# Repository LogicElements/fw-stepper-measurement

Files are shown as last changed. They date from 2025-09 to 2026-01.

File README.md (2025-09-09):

# Stepper Measurement System

This repository contains hardware and firmware for the Stepper Measurement System:
 - Hardware board 
 - Bootloader
 - Application firmware
 - Python test scripts
 - Documentation

# Register map

Modbus register map and internal memory structure is managed using Excel generator
./Documents/PrecRtdSim.xlsm. This worksheet contains several VBA scripts that
translates defined variables into firmware local storage definition, firmware modbus
register map, python class definition and json register map definition.

Some documentation can be found in ./Documents/wiki.

> [!NOTE]
> Opening excel worksheet with macros may show some kind of warning

# Programming bootloader

In order to flash bootloader firmware with serial number, proceed as follows:
- connect power and st-link
- edit ./Binary/STLink-program.bat with serial number prefix and binary names
- run `./Binary/STLink-program.bat x` where `x` is serial number to program 

Any further debugging can be done using IDE.

# Python tools

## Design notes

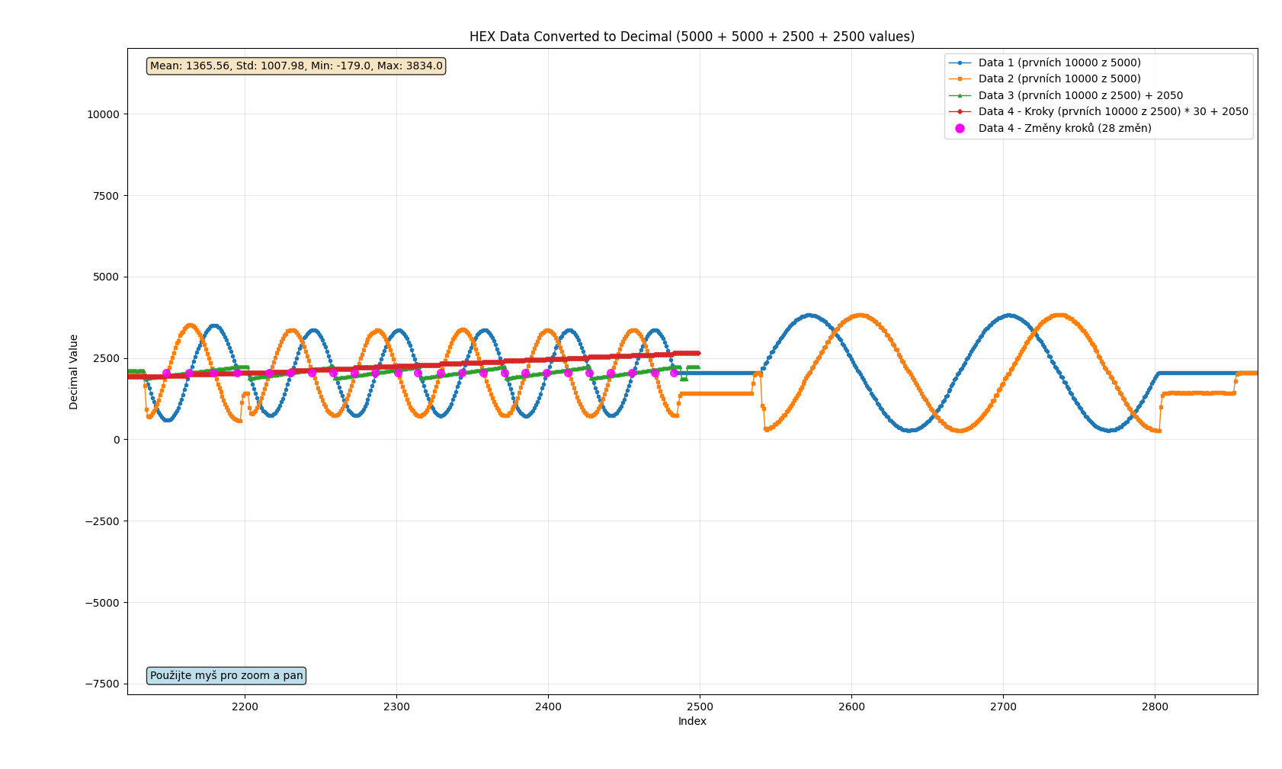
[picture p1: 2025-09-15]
Documents/img/doraz_komplet.png

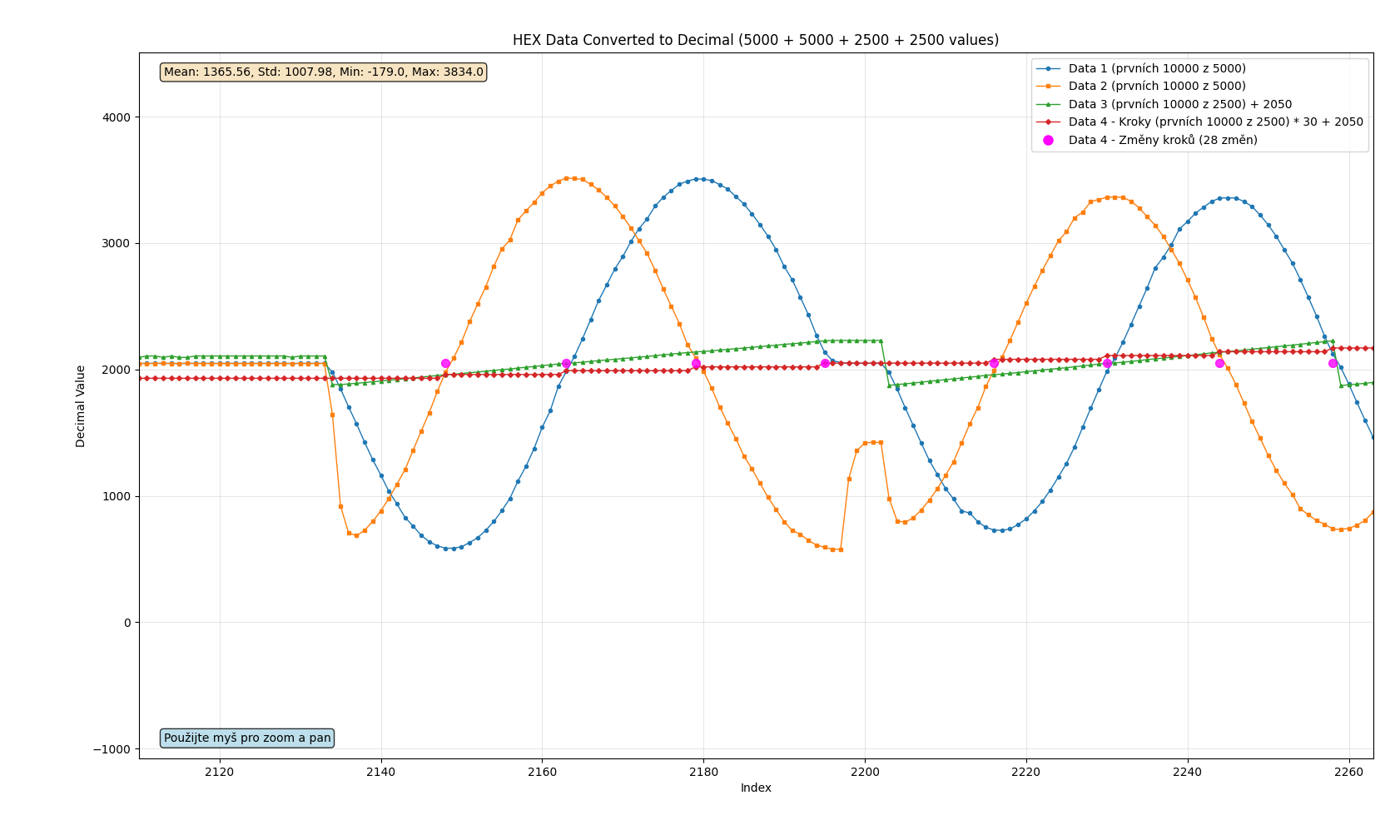
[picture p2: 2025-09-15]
Documents/img/doraz_cast_prubehu.png

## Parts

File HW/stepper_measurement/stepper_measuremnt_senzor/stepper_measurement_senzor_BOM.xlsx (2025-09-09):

Comment | Description | Designator | Footprint | LibRef | Quantity | Link
0.1uF | Capacitor | C4.1, C4.2, C4.3, C4.4, C6.1, C6.2, C6.3, C6.4, C7.1, C7.2, C7.3, C7.4 | SMD_CAPACITOR_0805 | Capacitor | 12 | https://cz.mouser.com/ProductDetail/KYOCERA-AVX/KAM21BR71H104JT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
 | Diode Schottky | D2.1, D2.2, D2.3, D2.4, D3.1, D3.2, D3.3, D3.4 | SMD_DO-214AChttps://cz.mouser.com/ProductDetail/Comchip-Technology/CZRA4728-HF?qs=2qJf6qQ4IOKpvgiXKvPuNQ%3D%3D | Diode_Schottky | 8 | https://cz.mouser.com/ProductDetail/Comchip-Technology/CZRA4728-HF?qs=2qJf6qQ4IOKpvgiXKvPuNQ%3D%3D
M50-3202045 | 1.27mm (0.05) Pitch DIL Horizontal Throughboard Socket Assembly, gold, 20+20 contacts | J1 | HARWIN_M50-3202045 | M50-3202045 | 1 | https://cz.mouser.com/ProductDetail/Harwin/M50-3202045?qs=Jph8NoUxIfXFh9Xgg1OEGQ%3D%3D
H2175-05 |  | J4, J5, J6, J7 | HARWIN_H2175-05 | H2175-05 | 4 | https://cz.mouser.com/ProductDetail/Harwin/H2175-05?qs=ulE8k0yEMYbNbWL6Op%252Bk7A%3D%3D
M50-3530242 | 1.27mm (0.05) Pitch SIL Vertical Throughboard Pin Header, selective gold + tin, 2 contacts | J8, J9, J10.1, J10.2, J10.3, J10.4 | HARWIN_M50-3530242 | M50-3530242 | 6 | https://cz.mouser.com/ProductDetail/Harwin/M50-3530242?qs=%252BdQmOuGyFcFfqfwYQe%2FxZw%3D%3D
Red | LED | LED1 | SMD_LED_0805 | LED | 1 | https://cz.mouser.com/ProductDetail/Wurth-Elektronik/150080RS75000
0.130 | Resistor | R3.1, R3.2, R3.3, R3.4 | SMD_RESISTOR_1206 | Resistor | 4 | https://cz.mouser.com/ProductDetail/TE-Connectivity-CGS/RLC73K2BR13FTDF
10K | Resistor | R10.1, R10.2, R10.3, R10.4, R11.1, R11.2, R11.3, R11.4 | SMD_RESISTOR_0805 | Resistor | 8 | https://cz.mouser.com/ProductDetail/TE-Connectivity-Holsworthy/4-2176238-9
1K | Resistor | R12, R15.1, R15.2, R15.3, R15.4 | SMD_RESISTOR_0805 | Resistor | 5 | https://cz.mouser.com/ProductDetail/Panasonic/ERA-6AED102V
6.5K | Resistor | R13.1, R13.2, R13.3, R13.4 | SMD_RESISTOR_0805 | Resistor | 4 | https://cz.mouser.com/ProductDetail/Panasonic/ERJ-HP6F6491V
12.4K | Resistor | R14.1, R14.2, R14.3, R14.4 | SMD_RESISTOR_0805 | Resistor | 4 | https://cz.mouser.com/ProductDetail/Panasonic/ERJ-UP6F1242V
50K | Resistor | R16.1, R16.2, R16.3, R16.4, R17.1, R17.2, R17.3, R17.4 | SMD_RESISTOR_0805 | Resistor | 8 | https://cz.mouser.com/ProductDetail/Vishay-Draloric/RCA08056K49FKEA
47K | Resistor | R18.1, R18.2, R18.3, R18.4, R19.1, R19.2, R19.3, R19.4 | SMD_RESISTOR_0805 | Resistor | 8 | https://cz.mouser.com/ProductDetail/Bourns/CRS0805-FX-4701ELF
INA240A1D | -4 to 80V, bidirectional, ultra-precise current sense amplifier with enhanced PWM rejection 8-SOIC -40 to 125 | U2.1, U2.2, U2.3, U2.4 | SOIC127P599X175-8N | INA240A1D | 4 | https://cz.mouser.com/ProductDetail/Texas-Instruments/INA240A1D?qs=u4fy%2FsgLU9OqCdP7Ou6Gjw%3D%3D
INA826AID | Precision, 200-Î¼A Supply Current, 36-V Supply Instrumentation Amplifier | U3.1, U3.2, U3.3, U3.4 | SOIC127P599X175-8N | INA826AID | 4 | https://cz.mouser.com/ProductDetail/Texas-Instruments/INA826AID?qs=RqytGdBYyUH0CDtkCzl1iw%3D%3D
 |  |  |  |  | 81

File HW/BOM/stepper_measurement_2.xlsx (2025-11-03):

Name | Description | Designator | Quantity | Supplier 1
2.2uF | Capacitor | C1, C24 | 2 | https://cz.mouser.com/ProductDetail/TDK/C2012X7R2A225K125AC?qs=17ckDYBRdekDf%2FwiwHq7Mg%3D%3D
100nF | Capacitor | C2, C4, C6, C11, C13, C14, C15, C16, C17, C18, C22, C23, C26, C27.1, C27.2, C28.1, C28.2, C29.1, C29.2 | 19 | https://cz.mouser.com/ProductDetail/KYOCERA-AVX/KAM21BR71H104JT?qs=Jm2GQyTW%2Fbic6Zk4McEt6w%3D%3D
10uF/1206 | Capacitor | C8, C9 | 2 | https://cz.mouser.com/ProductDetail/TAIYO-YUDEN/MLASU31LBB5106KTNA01?qs=tlsG%2FOw5FFhl%2FyO8kWYY2Q%3D%3D
10uF | Capacitor | C3, C5, C7, C10 | 4 | https://cz.mouser.com/ProductDetail/TAIYO-YUDEN/GMK212BBJ106KG-T?qs=VWNNG7jHlrKFQEsXPkGH1A%3D%3D
4.7uF | Capacitor | C12 | 1 | https://cz.mouser.com/ProductDetail/Murata-Electronics/GCM21BC71E475KE36K?qs=dNBNMwHp2UBfaO4Bu7xrag%3D%3D
1uF | Capacitor | C19, C25 | 2 | https://cz.mouser.com/ProductDetail/TAIYO-YUDEN/MCAST21GSB7105MTNB25?qs=tlsG%2FOw5FFgklVSELtG1Zg%3D%3D
1pF | Capacitor | C20, C21 | 2 | https://cz.mouser.com/ProductDetail/Vishay-Vitramon/VJ0805D0R1BXPAJHT?qs=HXFqYaX1Q2ys%2Fz3sbYQ8tQ%3D%3D
 | Diode Schottky | D1 | 1 | https://cz.mouser.com/ProductDetail/Vishay-General-Semiconductor/B360A-M3-61T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
SMAJ13CA | 27.2V Clamp 85A (8/20Âµs) Ipp Tvs Diode Surface Mount DO-214AC (SMA) | D2, D3 | 2 | https://cz.mouser.com/ProductDetail/Bourns/SMAJ13CA?qs=A3H9pljuJ8RfXOL6JRK7RQ%3D%3D
FBMJ2125HM330-T | 33 Ohms @ 100MHz 1 Power Line Ferrite Bead 0805 (2012 Metric) 4A 8mOhm | FB1, FB2, FB3, FB4, FB5 | 5 | https://cz.mouser.com/ProductDetail/TAIYO-YUDEN/FBMJ2125HM330-T?qs=I6KAKw0tg2x2oSHkK0gl%252Bw%3D%3D
LMR51610YFDBVR | Integrated Circuit | IC1 | 1 | https://cz.mouser.com/ProductDetail/Texas-Instruments/LMR51610YFDBVR?qs=dbcCsuKDzFWbILGJVHCR7g%3D%3D
1725669 | PCB Terminal Screw 2.54mm 20AWG 160V 6A 3 Position COMBICON MPT Series | Phoenix Contact 1725669 | J1 | 1 | https://cz.mouser.com/ProductDetail/Phoenix-Contact/1725669?qs=A%2FKWGUWTCZjmkTL0Oe91ew%3D%3D
1725656 | PCB Terminal Screw 2.54mm 20AWG 160V 6A 2 Position COMBICON MPT Series | Phoenix Contact 1725656 | J2, J5 | 2 | https://cz.mouser.com/ProductDetail/Phoenix-Contact/1725656
M50-3530342 |  | J3 | 1 | https://cz.mouser.com/ProductDetail/Harwin/M50-3530342?qs=%252BdQmOuGyFcFOxjGK%2F4HnAg%3D%3D
1725711 |  | J4 | 1 | https://cz.mouser.com/ProductDetail/Phoenix-Contact/1725711?qs=W3wJikR1%252BS7n1cN8b%252BRI%2FQ%3D%3D
BD125-10-A-0305-0580-L-B | Connector Header Surface Mount 10 position 0.050 (1.27mm) | J6 | 1 | https://cz.mouser.com/ProductDetail/GCT/BD125-10-A-0305-0580-L-B?qs=amGC7iS6iy%252BPUE%252B5wV8wFA%3D%3D
10uH | High Current Shielded Power Inductor | 33uH | 18A | 1LN | 7.3 x 6.8 x 3mm Footprint | 3mm Height Profile | L1 | 1 | https://cz.mouser.com/ProductDetail/ABRACON/AMDLA7030S-100MT?qs=DPoM0jnrROV93kSaO1eR7w%3D%3D
Red | LED | LED1 | 1 | https://cz.mouser.com/ProductDetail/Kingbright/APT2012PGW
Blue | LED | LED2 | 1 | https://cz.mouser.com/ProductDetail/VCC/VAOL-S8SB4
22.1K | Resistor | R1 | 1 | https://cz.mouser.com/ProductDetail/Panasonic/ERA-6ARB2212V
118K | Resistor | R2 | 1 | https://cz.mouser.com/ProductDetail/KOA-Speer/RK73H2ARTTD1183D
1K | Resistor | R3, R9, R17.1, R17.2 | 4 | https://cz.mouser.com/ProductDetail/Panasonic/ERA-6AED102V
10K | Resistor | R4, R7, R8, R10, R11.1, R11.2 | 6 | https://cz.mouser.com/ProductDetail/Panasonic/ERJ-6RBD103V?qs=sGAEpiMZZMtG0KNrPCHnjWXb3yLuGJ27mHWFHZHNGq0%3D
22 | Resistor | R5, R6 | 2 | https://cz.mouser.com/ProductDetail/Vishay/CRCW080522R0JNEAC
13.5K | Resistor | R12.1, R12.2 | 2 | https://cz.mouser.com/ProductDetail/YAGEO/RT0805FRE0713K3L?qs=sGAEpiMZZMtG0KNrPCHnjTg0x5DoQJ5PuHW6D4puiu0%3D
51K | Resistor | R13.1, R13.2, R14.1, R14.2 | 4 | https://cz.mouser.com/ProductDetail/Panasonic/ERJ-UP6D5102V
6.5K | Resistor | R15.1, R15.2 | 2 | https://cz.mouser.com/ProductDetail/Vishay-Draloric/RCA08056K49FKEA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
510K | Resistor | R16.1, R16.2 | 2 | https://cz.mouser.com/ProductDetail/Panasonic/ERJ-UP6D5103V?qs=sGAEpiMZZMtlubZbdhIBIKPMpJOYNEkDcCejZvBtHWA%3D
47K | Resistor | R18.1, R18.2, R19.1, R19.2 | 4 | https://cz.mouser.com/ProductDetail/Panasonic/ERA-6ARW473V?qs=sGAEpiMZZMtlubZbdhIBIJiMSTY83nT4JN0dI94XAHw%3D
R090 | Resistor | R20.1, R20.2 | 2 | https://cz.mouser.com/ProductDetail/Panasonic/ERJ-L08UF90MV?qs=22lEN67Lqx7gT21Gs2Glcw%3D%3D
204-6ST | Switch | S1 | 1 | https://cz.mouser.com/ProductDetail/CTS-Electronic-Components/204-6ST?qs=qNzHFtQhdJ8m4uCdOMmOPg%3D%3D
PTS636_SM43J_SMTR_LFS | Tactile Switch SPST-NO Top Actuated Surface Mount | S2, S3 | 2 | https://cz.mouser.com/ProductDetail/CK/PTS636SM43JSMTR-LFS?qs=%252BXxaIXUDbq0c6yfQESkQsA%3D%3D
SPX1117M3-L-3-3/TR | Linear Voltage Regulator IC Positive Fixed 1 Output 800mA SOT-223 | U1 | 1 | https://cz.mouser.com/ProductDetail/MaxLinear/SPX1117M3-L-3-3-TR?qs=S%2FCBhQS5rCofor8XCFP4ag%3D%3D
SN65HVD72D | 3.3-V half-duplex RS-485 with IEC ESD, 250 kbps 8-SOIC -40 to 125 | U2 | 1 | https://cz.mouser.com/ProductDetail/Texas-Instruments/SN65HVD72D?qs=umApKWeh9pW%2FHHD2rvNVAg%3D%3D
STM32F446RET6TR | ARMÂ® CortexÂ®-M4 series Microcontroller IC 32-Bit Single-Core 180MHz 512KB (512K x 8) FLASH 64-LQFP (10x10) | U3 | 1 | https://cz.mouser.com/ProductDetail/STMicroelectronics/STM32F446RET6TR?qs=xZ%2FP%252Ba9zWqYaBJrnMqQZtg%3D%3D
INA826AID | Precision, 200-Î¼A Supply Current, 36-V Supply Instrumentation Amplifier | U4.1, U4.2 | 2 | https://cz.mouser.com/ProductDetail/Texas-Instruments/INA826AID?qs=RqytGdBYyUH0CDtkCzl1iw%3D%3D
INA240A1D | -4 to 80V, bidirectional, ultra-precise current sense amplifier with enhanced PWM rejection 8-SOIC -40 to 125 | U5.1, U5.2 | 2 | https://cz.mouser.com/ProductDetail/Texas-Instruments/INA240A1D?qs=u4fy%2FsgLU9OqCdP7Ou6Gjw%3D%3D
VJ13MC0600KBA | 75 V 250 A Varistor 1 Circuit Surface Mount, MLCV 1210 (3225 Metric) | V1 | 1 | https://cz.mouser.com/ProductDetail/KYOCERA-AVX/VJ13MC0600KBA?qs=rJDJZBleyzDTqFzBX7haAw%3D%3D
XRCGB26M000F3N00R0 | 26 MHz Â±30ppm Crystal 6pF 150 Ohms 4-SMD, No Lead | Y1 | 1 | https://cz.mouser.com/ProductDetail/Murata-Electronics/XRCGB26M000F3N00R0?qs=r3UZegS7eeoL8i5Fyo9Miw%3D%3D
Krabička | ---- | ----- | 1 | https://www.tme.eu/cz/details/it-35.0207000.bl/krabicky-na-listu-din/italtronic/35-0207000-bl/

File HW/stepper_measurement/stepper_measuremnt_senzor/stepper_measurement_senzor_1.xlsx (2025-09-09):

Comment | Description | Designator | Footprint | LibRef | Quantity
0.1uF | Capacitor | C4.1, C4.2, C4.3, C4.4, C6.1, C6.2, C6.3, C6.4, C7.1, C7.2, C7.3, C7.4 | SMD_CAPACITOR_0805 | Capacitor | 12
 | Diode Schottky | D2.1, D2.2, D2.3, D2.4, D3.1, D3.2, D3.3, D3.4 | SMD_DO-214AC | Diode_Schottky | 8
M50-3202045 | 1.27mm (0.05) Pitch DIL Horizontal Throughboard Socket Assembly, gold, 20+20 contacts | J1 | HARWIN_M50-3202045 | M50-3202045 | 1
H2175-05 |  | J4, J5, J6, J7 | HARWIN_H2175-05 | H2175-05 | 4
M50-3530242 | 1.27mm (0.05) Pitch SIL Vertical Throughboard Pin Header, selective gold + tin, 2 contacts | J8, J9, J10.1, J10.2, J10.3, J10.4 | HARWIN_M50-3530242 | M50-3530242 | 6
Red | LED | LED1 | SMD_LED_0805 | LED | 1
0.130 | Resistor | R3.1, R3.2, R3.3, R3.4 | SMD_RESISTOR_1206 | Resistor | 4
10K | Resistor | R10.1, R10.2, R10.3, R10.4, R11.1, R11.2, R11.3, R11.4 | SMD_RESISTOR_0805 | Resistor | 8
1K | Resistor | R12, R15.1, R15.2, R15.3, R15.4 | SMD_RESISTOR_0805 | Resistor | 5
6.5K | Resistor | R13.1, R13.2, R13.3, R13.4 | SMD_RESISTOR_0805 | Resistor | 4
12.4K | Resistor | R14.1, R14.2, R14.3, R14.4 | SMD_RESISTOR_0805 | Resistor | 4
50K | Resistor | R16.1, R16.2, R16.3, R16.4, R17.1, R17.2, R17.3, R17.4 | SMD_RESISTOR_0805 | Resistor | 8
47K | Resistor | R18.1, R18.2, R18.3, R18.4, R19.1, R19.2, R19.3, R19.4 | SMD_RESISTOR_0805 | Resistor | 8
INA240A1D | -4 to 80V, bidirectional, ultra-precise current sense amplifier with enhanced PWM rejection 8-SOIC -40 to 125 | U2.1, U2.2, U2.3, U2.4 | SOIC127P599X175-8N | INA240A1D | 4
INA826AID | Precision, 200-Î¼A Supply Current, 36-V Supply Instrumentation Amplifier | U3.1, U3.2, U3.3, U3.4 | SOIC127P599X175-8N | INA826AID | 4

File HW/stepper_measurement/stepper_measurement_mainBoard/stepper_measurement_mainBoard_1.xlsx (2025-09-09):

Line # | Name | Description | Designator | Quantity | Footprint | Link
 | 2.2uF | Capacitor | C1, C24 | 2 | SMD_CAPACITOR_0805 | https://cz.mouser.com/ProductDetail/TDK/C2012X7R2A225K125AC?qs=17ckDYBRdekDf%2FwiwHq7Mg%3D%3D
 | 0.1uF | Capacitor | C2 | 1 | SMD_CAPACITOR_0805 | https://cz.mouser.com/ProductDetail/KYOCERA-AVX/KAF21KR72A104KL?qs=Jm2GQyTW%2FbiUCISqVwD%2FLA%3D%3D
 | 10uF | Capacitor | C3, C5, C6, C10 | 4 | SMD_CAPACITOR_0805 | https://cz.mouser.com/ProductDetail/TAIYO-YUDEN/GMK212BBJ106KG-T?qs=VWNNG7jHlrKFQEsXPkGH1A%3D%3D
 | 100nF | Capacitor | C4, C7, C11, C13, C14, C15, C16, C17, C18, C22, C23, C26 | 12 | SMD_CAPACITOR_0805 | https://cz.mouser.com/ProductDetail/KYOCERA-AVX/KAM21BR71H104JT?qs=Jm2GQyTW%2Fbic6Zk4McEt6w%3D%3D
 | 10uF | 4.7 ÂµF Â±10% 100V Ceramic Capacitor X7S 1210 (3225 Metric) | C8, C9 | 2 | CAPC3225X280N | https://cz.mouser.com/ProductDetail/Murata-Electronics/GRM32EC72A106ME05K?qs=d0WKAl%252BL4KZhKlQa6BdBQA%3D%3D
 | 4.7uF | Capacitor | C12 | 1 | SMD_CAPACITOR_0805 | https://cz.mouser.com/ProductDetail/Murata-Electronics/GCM21BC71E475KE36K?qs=dNBNMwHp2UBfaO4Bu7xrag%3D%3D
 | 1uF | Capacitor | C19, C25 | 2 | SMD_CAPACITOR_0805 | https://cz.mouser.com/ProductDetail/TAIYO-YUDEN/MCAST21GSB7105MTNB25?qs=tlsG%2FOw5FFgklVSELtG1Zg%3D%3D
 | 1pF | Capacitor | C20, C21 | 2 | SMD_CAPACITOR_0805 | https://cz.mouser.com/ProductDetail/Vishay-Vitramon/VJ0805D0R1BXPAJHT?qs=HXFqYaX1Q2ys%2Fz3sbYQ8tQ%3D%3D
 |  | Diode Schottky | D1 | 1 | SMD_DO-214AC | https://cz.mouser.com/ProductDetail/Vishay-General-Semiconductor/B360A-M3-61T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
 | SMAJ13CA | 27.2V Clamp 85A (8/20Âµs) Ipp Tvs Diode Surface Mount DO-214AC (SMA) | D2, D3 | 2 | DIOM4325X250N | https://cz.mouser.com/ProductDetail/Bourns/SMAJ13CA?qs=A3H9pljuJ8RfXOL6JRK7RQ%3D%3D
 | FBMJ2125HM330-T | 33 Ohms @ 100MHz 1 Power Line Ferrite Bead 0805 (2012 Metric) 4A 8mOhm | FB1, FB2, FB3, FB4, FB5 | 5 | BEADC2012X105N | https://cz.mouser.com/ProductDetail/TAIYO-YUDEN/FBMJ2125HM330-T?qs=I6KAKw0tg2x2oSHkK0gl%252Bw%3D%3D
 | LMR51610YFDBVR | Integrated Circuit | IC1 | 1 | SOT95P280X145-6N | https://cz.mouser.com/ProductDetail/Texas-Instruments/LMR51610YFDBVR?qs=dbcCsuKDzFWbILGJVHCR7g%3D%3D
 | 1725669 | PCB Terminal Screw 2.54mm 20AWG 160V 6A 3 Position COMBICON MPT Series | Phoenix Contact 1725669 | J1 | 1 | PHOENIX_1725669 | https://cz.mouser.com/ProductDetail/Phoenix-Contact/1725669?qs=A%2FKWGUWTCZjmkTL0Oe91ew%3D%3D
 | 1725656 | PCB Terminal Screw 2.54mm 20AWG 160V 6A 2 Position COMBICON MPT Series | Phoenix Contact 1725656 | J2, J7 | 2 | PHOENIX_1725656 | https://cz.mouser.com/ProductDetail/Phoenix-Contact/1725656
 | M50-3530342 |  | J3 | 1 | HARWIN_M50-3530342 | https://cz.mouser.com/ProductDetail/Harwin/M50-3530342?qs=%252BdQmOuGyFcFOxjGK%2F4HnAg%3D%3D
 | M50-3902042 |  | J4 | 1 | HARWIN_M50-3902042 | https://cz.mouser.com/ProductDetail/Harwin/M50-3902042?qs=9fQaSFfsqswzCa6Gw0v0Zw%3D%3D
 | 1725711 |  | J5, J6 | 2 | PHOENIX_1725711 | https://cz.mouser.com/ProductDetail/Phoenix-Contact/1725711?qs=W3wJikR1%252BS7n1cN8b%252BRI%2FQ%3D%3D
 | BD125-10-A-0305-0580-L-B | Connector Header Surface Mount 10 position 0.050 (1.27mm) | J8 | 1 | GCT_BD125-10-A-0305-0580-L-B | https://cz.mouser.com/ProductDetail/GCT/BD125-10-A-0305-0580-L-B?qs=amGC7iS6iy%252BPUE%252B5wV8wFA%3D%3D
 | 10uH | High Current Shielded Power Inductor | 33uH | 18A | 1LN | 7.3 x 6.8 x 3mm Footprint | 3mm Height Profile | L1 | 1 | IND_F1D1-060603W-R47M | https://cz.mouser.com/ProductDetail/ABRACON/AMDLA7030S-100MT?qs=DPoM0jnrROV93kSaO1eR7w%3D%3D
 | Red | LED | LED1 | 1 | SMD_LED_0805
 | Blue | LED | LED2 | 1 | SMD_LED_0805
 | 22.1K | Resistor | R1 | 1 | SMD_RESISTOR_0805 | https://cz.mouser.com/ProductDetail/Panasonic/ERA-6ARB2212V
 | 118K | Resistor | R2 | 1 | SMD_RESISTOR_0805 | https://cz.mouser.com/ProductDetail/KOA-Speer/RK73H2ARTTD1183D
 | 1K | Resistor | R3, R9 | 2 | SMD_RESISTOR_0805 | https://cz.mouser.com/ProductDetail/Panasonic/ERA-6AED102V
 | 10K | Resistor | R4, R7, R8, R10 | 4 | SMD_RESISTOR_0805 | https://cz.mouser.com/ProductDetail/Panasonic/ERJ-6RBD103V?qs=sGAEpiMZZMtG0KNrPCHnjWXb3yLuGJ27mHWFHZHNGq0%3D
 | 22 | Resistor | R5, R6 | 2 | SMD_RESISTOR_0805 | https://cz.mouser.com/ProductDetail/Vishay-Dale/CRCW080522R0JNEAC
 | 204-6ST | Switch | S1 | 1 | 2046ST | https://cz.mouser.com/ProductDetail/CTS-Electronic-Components/204-6ST?qs=qNzHFtQhdJ8m4uCdOMmOPg%3D%3D
 | PTS636_SM43J_SMTR_LFS | Tactile Switch SPST-NO Top Actuated Surface Mount | S2, S3 | 2 | SW_PTS636_SM43J_SMTR_LFS | https://cz.mouser.com/ProductDetail/CK/PTS636SM43JSMTR-LFS?qs=%252BXxaIXUDbq0c6yfQESkQsA%3D%3D
 | SPX1117M3-L-3-3/TR | Linear Voltage Regulator IC Positive Fixed 1 Output 800mA SOT-223 | U1 | 1 | SOT230P700X180-3N | https://cz.mouser.com/ProductDetail/MaxLinear/SPX1117M3-L-3-3-TR?qs=S%2FCBhQS5rCofor8XCFP4ag%3D%3D
 | SN65HVD72D | 3.3-V half-duplex RS-485 with IEC ESD, 250 kbps 8-SOIC -40 to 125 | U2 | 1 | SOIC127P599X175-8N | https://cz.mouser.com/ProductDetail/Texas-Instruments/SN65HVD72D?qs=umApKWeh9pW%2FHHD2rvNVAg%3D%3D
 | STM32F446RET6TR | ARMÂ® CortexÂ®-M4 series Microcontroller IC 32-Bit Single-Core 180MHz 512KB (512K x 8) FLASH 64-LQFP (10x10) | U3 | 1 | QFP50P1200X1200X160-64N | https://cz.mouser.com/ProductDetail/STMicroelectronics/STM32F446RET6TR?qs=xZ%2FP%252Ba9zWqYaBJrnMqQZtg%3D%3D
 | VJ13MC0600KBA | 75 V 250 A Varistor 1 Circuit Surface Mount, MLCV 1210 (3225 Metric) | V1 | 1 | VAR_VJ13MC0600KBA | https://cz.mouser.com/ProductDetail/KYOCERA-AVX/VJ13MC0600KBA?qs=rJDJZBleyzDTqFzBX7haAw%3D%3D
 | XRCGB26M000F3N00R0 | 26 MHz Â±30ppm Crystal 6pF 150 Ohms 4-SMD, No Lead | Y1 | 1 | OSC_XRCGB26M000F3N00R0 | https://cz.mouser.com/ProductDetail/Murata-Electronics/XRCGB26M000F3N00R0?qs=r3UZegS7eeoL8i5Fyo9Miw%3D%3D
 |  |  |  | 64

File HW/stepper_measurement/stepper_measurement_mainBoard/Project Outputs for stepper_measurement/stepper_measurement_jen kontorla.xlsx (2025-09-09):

Comment | Description | Designator | Quantity | LibRef | Footprint
100uF | 100ÂµF 35V ì•Œë£¨ë¯¸ëŠ„ ì „í•´ ì»¤íŒ¨ì‹œí„° ë°©ì‚¬í˜•, ìº” - SMD 260mOhm @ 100kHz 2000 Hrs @ 105Â°C | C1 | 1 | EEEFT1V101AP | CAP_EEEFT1V101AP
2.2uF | Capacitor | C2 | 1 | Capacitor | SMD_CAPACITOR_0805
100nF | Capacitor | C3 | 1 | Capacitor | SMD_CAPACITOR_0805
10uF | Capacitor | C4 | 1 | Capacitor | SMD_CAPACITOR_0805
10uF | Capacitor | C5 | 1 | Capacitor | SMD_CAPACITOR_0805
100nF | Capacitor | C6 | 1 | Capacitor | SMD_CAPACITOR_0805
2.2uF | Capacitor | C7 | 1 | Capacitor | SMD_CAPACITOR_0805
100nF | Capacitor | C8 | 1 | Capacitor | SMD_CAPACITOR_0805
0.1uF | Capacitor | C9 | 1 | Capacitor | SMD_CAPACITOR_0805
4.7uF | Capacitor | C10 | 1 | Capacitor | SMD_CAPACITOR_0805
10uF | Capacitor | C11 | 1 | Capacitor | SMD_CAPACITOR_0805
100nF | Capacitor | C12 | 1 | Capacitor | SMD_CAPACITOR_0805
10uF | Capacitor | C13 | 1 | Capacitor | SMD_CAPACITOR_0805
10uF | Capacitor | C14 | 1 | Capacitor | SMD_CAPACITOR_0805
100nF | Capacitor | C15 | 1 | Capacitor | SMD_CAPACITOR_0805
100nF | Capacitor | C16 | 1 | Capacitor | SMD_CAPACITOR_0805
4.7uF | Capacitor | C17 | 1 | Capacitor | SMD_CAPACITOR_0805
100nF | Capacitor | C18 | 1 | Capacitor | SMD_CAPACITOR_0805
100nF | Capacitor | C19 | 1 | Capacitor | SMD_CAPACITOR_0805
100nF | Capacitor | C20 | 1 | Capacitor | SMD_CAPACITOR_0805
100nF | Capacitor | C21 | 1 | Capacitor | SMD_CAPACITOR_0805
100nF | Capacitor | C22 | 1 | Capacitor | SMD_CAPACITOR_0805
100nF | Capacitor | C23 | 1 | Capacitor | SMD_CAPACITOR_0805
1uF | Capacitor | C24 | 1 | Capacitor | SMD_CAPACITOR_0805
2.2uF | Capacitor | C25 | 1 | Capacitor | SMD_CAPACITOR_0805
2.2uF | Capacitor | C26 | 1 | Capacitor | SMD_CAPACITOR_0805
1uF | Capacitor | C27 | 1 | Capacitor | SMD_CAPACITOR_0805
100nF | Capacitor | C28 | 1 | Capacitor | SMD_CAPACITOR_0805
22uF | Capacitor | C29 | 1 | Capacitor | SMD_CAPACITOR_0805
100nF | Capacitor | C30 | 1 | Capacitor | SMD_CAPACITOR_0805
100nF | Capacitor | C31 | 1 | Capacitor | SMD_CAPACITOR_0805
1pF | Capacitor | C32 | 1 | Capacitor | SMD_CAPACITOR_0805
1pF | Capacitor | C33 | 1 | Capacitor | SMD_CAPACITOR_0805
SMAJ13CA | 27.2V Clamp 85A (8/20Âµs) Ipp Tvs Diode Surface Mount DO-214AC (SMA) | D1 | 1 | SMAJ13CA | DIOM4325X250N
SMAJ13CA | 27.2V Clamp 85A (8/20Âµs) Ipp Tvs Diode Surface Mount DO-214AC (SMA) | D2 | 1 | SMAJ13CA | DIOM4325X250N
 | Diode Schottky | D3 | 1 | Diode_Schottky | SMD_DO-214AC
SS1H10-E3/61T | Diode Schottky | D4 | 1 | Diode_Schottky | SMD_DO-214AC
FBMJ2125HM330-T | 33 Ohms @ 100MHz 1 Power Line Ferrite Bead 0805 (2012 Metric) 4A 8mOhm | FB1 | 1 | FBMJ2125HM330-T | BEADC2012X105N
FBMJ2125HM330-T | 33 Ohms @ 100MHz 1 Power Line Ferrite Bead 0805 (2012 Metric) 4A 8mOhm | FB2 | 1 | FBMJ2125HM330-T | BEADC2012X105N
FBMJ2125HM330-T | 33 Ohms @ 100MHz 1 Power Line Ferrite Bead 0805 (2012 Metric) 4A 8mOhm | FB3 | 1 | FBMJ2125HM330-T | BEADC2012X105N
FBMJ2125HM330-T | 33 Ohms @ 100MHz 1 Power Line Ferrite Bead 0805 (2012 Metric) 4A 8mOhm | FB4 | 1 | FBMJ2125HM330-T | BEADC2012X105N
MP9486AGN-Z | Buck Switching Regulator IC Positive Fixed 5V 1 Output 1A 8-SOIC (0.154, 3.90mm Width) Exposed Pad | IC1 | 1 | MP9486AGN-Z | SOIC127P600X170-9N
STM32F429VGT6 | Integrated Circuit | IC2 | 1 | STM32F429VGT6 | QFP50P1600X1600X160-100N
1725669 | PCB Terminal Screw 2.54mm 20AWG 160V 6A 3 Position COMBICON MPT Series | Phoenix Contact 1725669 | J1 | 1 | 1725669 | PHOENIX_1725669
M50-3902042 |  | J2 | 1 | M50-3902042 | HARWIN_M50-3902042
BD125-10-A-0305-0580-L-B | Connector Header Surface Mount 10 position 0.050 (1.27mm) | J3 | 1 | BD125-10-A-0305-0580-L-B | GCT_BD125-10-A-0305-0580-L-B
1725711 |  | J4 | 1 | 1725711 | PHOENIX_1725711
1725656 | PCB Terminal Screw 2.54mm 20AWG 160V 6A 2 Position COMBICON MPT Series | Phoenix Contact 1725656 | J5 | 1 | 1725656 | PHOENIX_1725656
1725711 |  | J6 | 1 | 1725711 | PHOENIX_1725711
1725656 | PCB Terminal Screw 2.54mm 20AWG 160V 6A 2 Position COMBICON MPT Series | Phoenix Contact 1725656 | J7 | 1 | 1725656 | PHOENIX_1725656
M50-3530342 |  | J8 | 1 | M50-3530342 | HARWIN_M50-3530342
F1D1-060603W-R47M | High Current Shielded Power Inductor | 0.47uH | 18A | 1LN | 7.3 x 6.8 x 3mm Footprint | 3mm Height Profile | L1 | 1 | F1D1-060603W-R47M | IND_F1D1-060603W-R47M
Blue | LED | LED1 | 1 | LED | SMD_LED_0805
Red | LED | LED2 | 1 | LED | SMD_LED_0805
240K | Resistor | R1 | 1 | Resistor | SMD_RESISTOR_0805
10K | Resistor | R2 | 1 | Resistor | SMD_RESISTOR_0805
10K | Resistor | R3 | 1 | Resistor | SMD_RESISTOR_0805
22 | Resistor | R4 | 1 | Resistor | SMD_RESISTOR_0805
22 | Resistor | R5 | 1 | Resistor | SMD_RESISTOR_0805
10K | Resistor | R6 | 1 | Resistor | SMD_RESISTOR_0805
10K | Resistor | R7 | 1 | Resistor | SMD_RESISTOR_0805
1K | Resistor | R8 | 1 | Resistor | SMD_RESISTOR_0805
1K | Resistor | R9 | 1 | Resistor | SMD_RESISTOR_0805
PTS636_SM43J_SMTR_LFS | Tactile Switch SPST-NO Top Actuated Surface Mount | S1 | 1 | PTS636_SM43J_SMTR_LFS | SW_PTS636_SM43J_SMTR_LFS
PTS636_SM43J_SMTR_LFS | Tactile Switch SPST-NO Top Actuated Surface Mount | S2 | 1 | PTS636_SM43J_SMTR_LFS | SW_PTS636_SM43J_SMTR_LFS
SN65HVD72D | 3.3-V half-duplex RS-485 with IEC ESD, 250 kbps 8-SOIC -40 to 125 | U1 | 1 | SN65HVD72D | SOIC127P599X175-8N
SPX1117M3-L-3-3/TR | Linear Voltage Regulator IC Positive Fixed 1 Output 800mA SOT-223 | U2 | 1 | SPX1117M3-L-3-3/TR | SOT230P700X180-3N
XRCGB26M000F3N00R0 | 26 MHz Â±30ppm Crystal 6pF 150 Ohms 4-SMD, No Lead | Y1 | 1 | XRCGB26M000F3N00R0 | OSC_XRCGB26M000F3N00R0

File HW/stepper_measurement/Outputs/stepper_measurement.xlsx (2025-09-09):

Line # | Name | Description | Designator | Quantity | Manufacturer 1 | Manufacturer Part Number 1 | Manufacturer Lifecycle 1 | Supplier 1 | Supplier Part Number 1 | Supplier Unit Price 1 | Supplier Subtotal 1
 | 100uF | 100ÂµF 35V ì•Œë£¨ë¯¸ëŠ„ ì „í•´ ì»¤íŒ¨ì‹œí„° ë°©ì‚¬í˜•, ìº” - SMD 260mOhm @ 100kHz 2000 Hrs @ 105Â°C | C1 | 1
 | 2.2uF | Capacitor | C2, C7, C25, C26 | 4
 | 100nF | Capacitor | C3, C6, C8, C12, C15, C16, C18, C19, C20, C21, C22, C23, C28, C30, C31 | 15
 | 10uF | Capacitor | C4, C5, C11, C13, C14 | 5
 | 0.1uF | Capacitor | C9 | 1
 | 4.7uF | Capacitor | C10, C17 | 2
 | 1uF | Capacitor | C24, C27 | 2
 | 22uF | Capacitor | C29 | 1
 | 1pF | Capacitor | C32, C33 | 2
 | SMAJ13CA | 27.2V Clamp 85A (8/20Âµs) Ipp Tvs Diode Surface Mount DO-214AC (SMA) | D1, D2 | 2
 |  | Diode Schottky | D3 | 1
 | SS1H10-E3/61T | Diode Schottky | D4 | 1
 | FBMJ2125HM330-T | 33 Ohms @ 100MHz 1 Power Line Ferrite Bead 0805 (2012 Metric) 4A 8mOhm | FB1, FB2, FB3, FB4 | 4
 | MP9486AGN-Z | Buck Switching Regulator IC Positive Fixed 5V 1 Output 1A 8-SOIC (0.154, 3.90mm Width) Exposed Pad | IC1 | 1
 | STM32F429VGT6 | Integrated Circuit | IC2 | 1
 | 1725669 | PCB Terminal Screw 2.54mm 20AWG 160V 6A 3 Position COMBICON MPT Series | Phoenix Contact 1725669 | J1 | 1
 | M50-3902042 |  | J2 | 1
 | BD125-10-A-0305-0580-L-B | Connector Header Surface Mount 10 position 0.050 (1.27mm) | J3 | 1
 | 1725711 |  | J4, J6 | 2
 | 1725656 | PCB Terminal Screw 2.54mm 20AWG 160V 6A 2 Position COMBICON MPT Series | Phoenix Contact 1725656 | J5, J7 | 2
 | M50-3530342 |  | J8 | 1
 | F1D1-060603W-R47M | High Current Shielded Power Inductor | 0.47uH | 18A | 1LN | 7.3 x 6.8 x 3mm Footprint | 3mm Height Profile | L1 | 1
 | Blue | LED | LED1 | 1
 | Red | LED | LED2 | 1
 | 240K | Resistor | R1 | 1
 | 10K | Resistor | R2, R3, R6, R7 | 4
 |  | Resistor | R4, R5 | 2
 | 1K | Resistor | R8, R9 | 2
 | PTS636_SM43J_SMTR_LFS | Tactile Switch SPST-NO Top Actuated Surface Mount | S1, S2 | 2
 | SN65HVD72D | 3.3-V half-duplex RS-485 with IEC ESD, 250 kbps 8-SOIC -40 to 125 | U1 | 1
 | SPX1117M3-L-3-3/TR | Linear Voltage Regulator IC Positive Fixed 1 Output 800mA SOT-223 | U2 | 1
 | XRCGB26M000F3N00R0 | 26 MHz Â±30ppm Crystal 6pF 150 Ohms 4-SMD, No Lead | Y1 | 1

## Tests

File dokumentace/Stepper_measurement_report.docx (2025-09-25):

Stepper measurement

Vypracoval: Roušal Štěpán

# 1.Úvod

Popis úkolu:

Cílem tohoto úkolu je navrhnout a vytvořit hardware s mikrokontrolérem STM32 a odpovídající firmware pro sledování buzení vinutí stejnosměrných krokových motorů bez Hallových senzorů. Měření bude probíhat pomocí vícekanálového ADC, který bude sledovat napětí a proud na obou vinutích motoru. Zařízení umožní připojení dvou motorů, tedy celkem čtyř vinutí.

Klíčové body úkolu:

1. Návrh a výroba hardwaru – výběr vhodného STM32 mikrokontroléru, návrh PCB a osazení komponent.
2. Implementace ADC měření – konfigurace a optimalizace měření napětí a proudu na vinutích motorů.
3. Zpracování a analýza dat – vytvoření algoritmu pro vyhodnocení chování motorů na základě naměřených hodnot:
  a. zejména počet kroků/mikro-kroků, který odpovídá průběhům proudů na vinutích,
  b. případně detekce dorazu motorů ze změny průběhů proudů a napětí.
4. Komunikace s PC nebo jiným zařízením – např. pomocí sběrnice Modbus, kterou často využíváme pro testovací nástroje.
5. Optimalizace – nastavení optimální vzorkovací frekvence, parametrů ADC, apod.
6. Testování a validace – ověření funkčnosti systému na reálných motorech, ladění softwaru a hardwaru.

# 2. Hardware

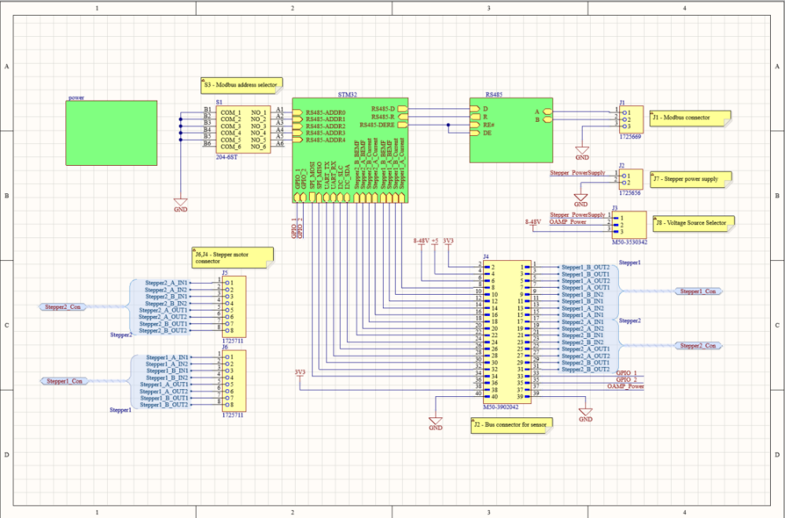
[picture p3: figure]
Obsah obrázku text, snímek obrazovky, diagram, Plán Obsah generovaný pomocí AI může být nesprávný.

Pro řízení byl použit mikrokontrolér STM32F446RET. Využívá se jeho 12bitový ADC převodník, konkrétně osm kanálů nastavených pro sledování napětí a proudu na vinutích motorů. Každé vinutí je tak měřeno dvojicí kanálů – jedním pro napětí a druhým pro proud. Díky tomuto uspořádání lze současně vyhodnocovat čtyři vinutí, tedy dva krokové motory, a na základě naměřených dat sledovat jejich chování. Proud je snímán pomocí shunt rezistorů se zesilovači, které upravují signál do rozsahu vhodného pro ADC.

Obrázek 1:Schéma propojení STM32 s měřicí částí

V současné fázi vývoje je zhotovena první verze zařízení, ve které je měřicí modul k hlavní desce připojen pomocí konektorů. Toto řešení umožňuje snadnější testování a případné úpravy zapojení bez nutnosti výroby nové desky. Zároveň poskytuje možnost rychlé výměny měřicí části nebo doplnění dalších variant zapojení při ladění.

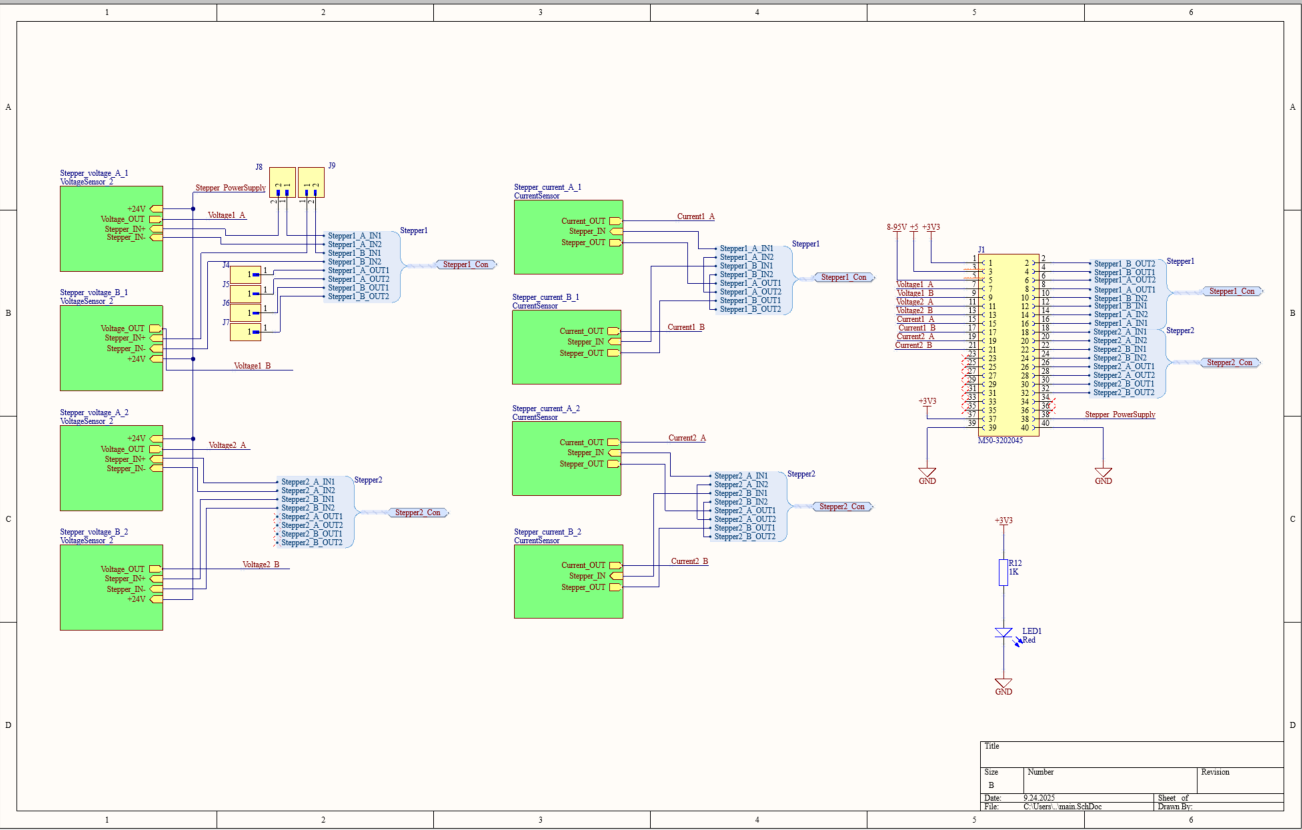
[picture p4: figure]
Obsah obrázku text, snímek obrazovky, diagram, Plán Obsah generovaný pomocí AI může být nesprávný.

Obrázek 2: Schéma zapojení měřicího modulu pro snímání napětí a proudu vinutí

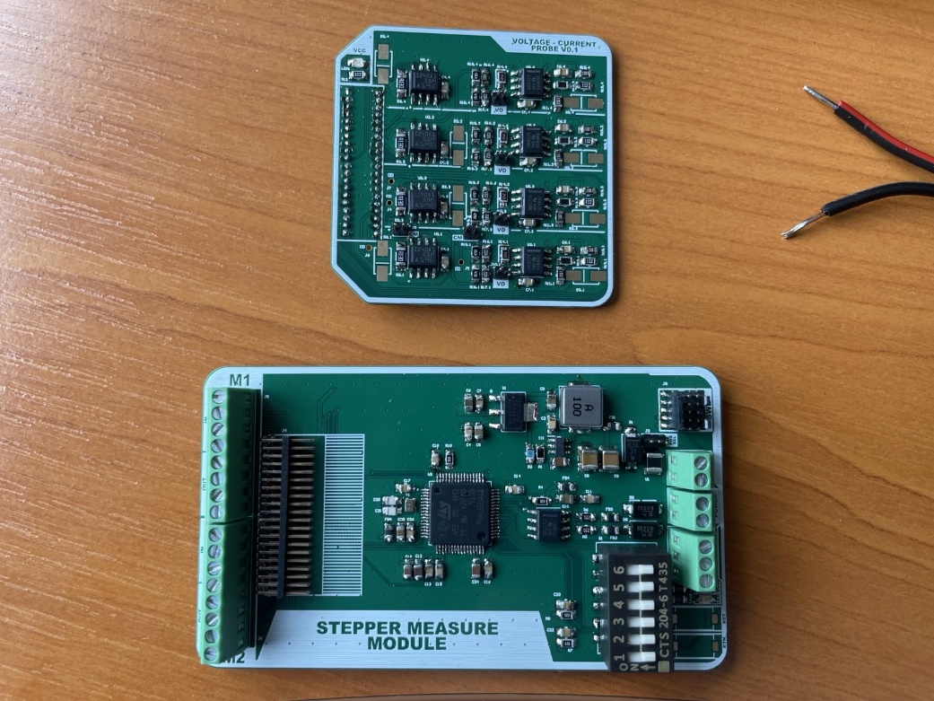
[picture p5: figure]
Obsah obrázku elektronika, Elektronická součástka, Obvodoví součástka, Elektronické inženýrství Obsah generovaný pomocí AI může být nesprávný.

Obrázek 3: Foto reálného HW

# 3. Zpracování dat

Měření proudů a napětí na vinutích motoru je řešeno pomocí vestavěného 12bitového ADC mikrokontroléru STM32. Využívají se čtyři kanály, kde dvojice vstupů vždy odpovídá jednomu vinutí – jeden kanál snímá proud a druhý napětí. Naměřená data jsou průběžně zpracovávána ve funkci obsluhy přerušení od DMA převodu.

Hodnoty z ADC procházejí filtrem kombinujícím exponenciální průměr a klouzavý průměr, aby se snížil vliv šumu. Z vyfiltrovaných proudů obou fází se počítá aktuální elektrický úhel motoru pomocí funkce atan2, který se převádí na stupně. Tento úhel je pak využit pro detekci kroků a směru otáčení. Algoritmus rozpoznává jednotlivé krokové polohy na základě definovaných úhlových mezí a při jejich dosažení inkrementuje nebo dekrementuje čítač kroků podle směru rotace.

Součástí měření je také sledování okamžiků, kdy proudy přecházejí nulou. V těchto okamžicích se ukládají odpovídající hodnoty napětí do vyrovnávací paměti, odkud se následně počítají jejich průměry. Tyto údaje lze využít k detekci mechanických dorazů nebo k analýze zatížení motoru.

Celý systém tak v reálném čase zajišťuje získávání a zpracování dat z vinutí motoru, filtraci signálů a odvozování parametrů, jako je počet kroků, směr otáčení a chování při zatížení.

# 4. Dosažené výsledky

Pro lepší analýzu výsledků jsou naměřené hodnoty z mikrokontroléru ukládány a následně zpracovávány pomocí jednoduché aplikace v Pythonu. Tato aplikace zajišťuje vykreslení průběhů proudů a napětí ve vinutích motoru.

Na následujícím grafu jsou zobrazeny průběhy signálů získané z měřicího modulu. Oranžová a modrá křivka představují naměřené hodnoty proudu ve vinutích motoru. Zelená křivka odpovídá výstupu funkce atan2, která z proudů obou fází počítá okamžitý úhel motoru. Tento úhel je následně využit k určení jednotlivých kroků a směru otáčení.

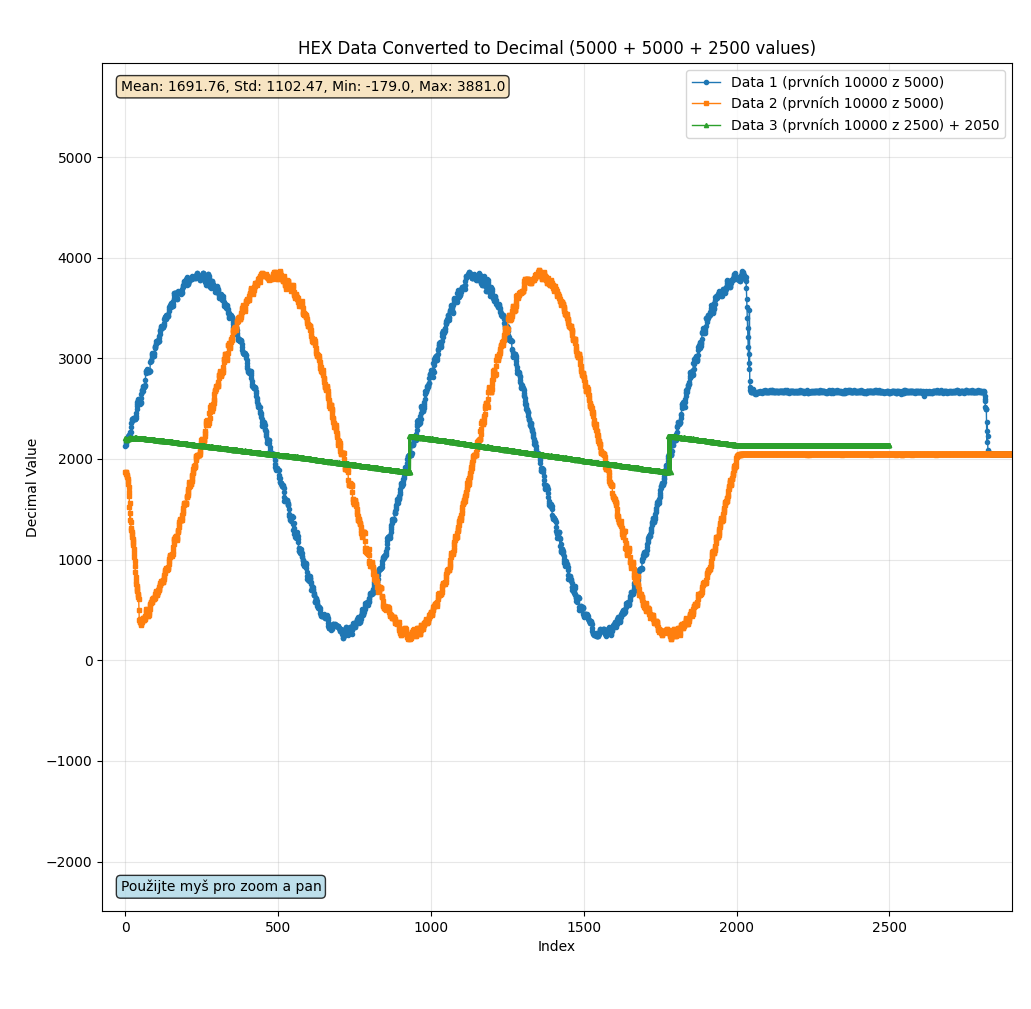
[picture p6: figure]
Obsah obrázku text, řada/pruh, Vykreslený graf, diagram Obsah generovaný pomocí AI může být nesprávný.

Obrázek 4: graf zobrazující průběhy proudů jednotlivými cívkami

Kromě toho firmware provádí také detekci dorazů pomocí sledování změn napětí na vinutích. Princip funguje tak, že pokud proud v cívce klesne k nule, začnou se do vyrovnávací paměti ukládat aktuální hodnoty napětí. Po nashromáždění dostatečného množství vzorků se z těchto dat vypočítá průměrná hodnota, na jejímž základě lze vyhodnotit, zda se motor nachází v mechanickém dorazu nebo pracuje v běžném režimu.

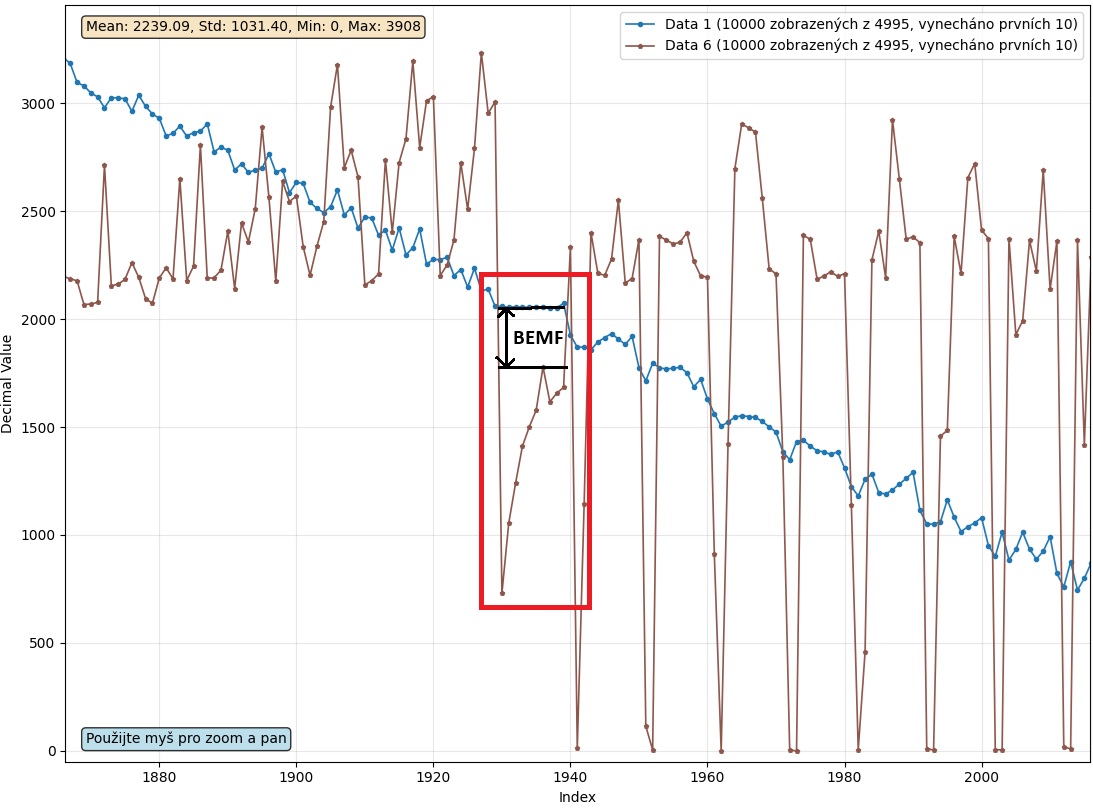
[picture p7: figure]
Obsah obrázku text, řada/pruh, diagram, Vykreslený graf Obsah generovaný pomocí AI může být nesprávný.

Na následujícím obrázku je uvedena ukázka z měření na jednom z vinutí motoru. Je zde patrný průběh proudu a napětí v okamžiku, kdy motor pracuje v normálním chodu. Při průchodu proudu nulou je zároveň možné pozorovat vznikající napětí zpětné elektromotorické síly (BEMF), které lze využít k vyhodnocení stavu motoru a dalšímu zpracování v algoritmu.

Obrázek 5: detekce BEMF při normálním provozu

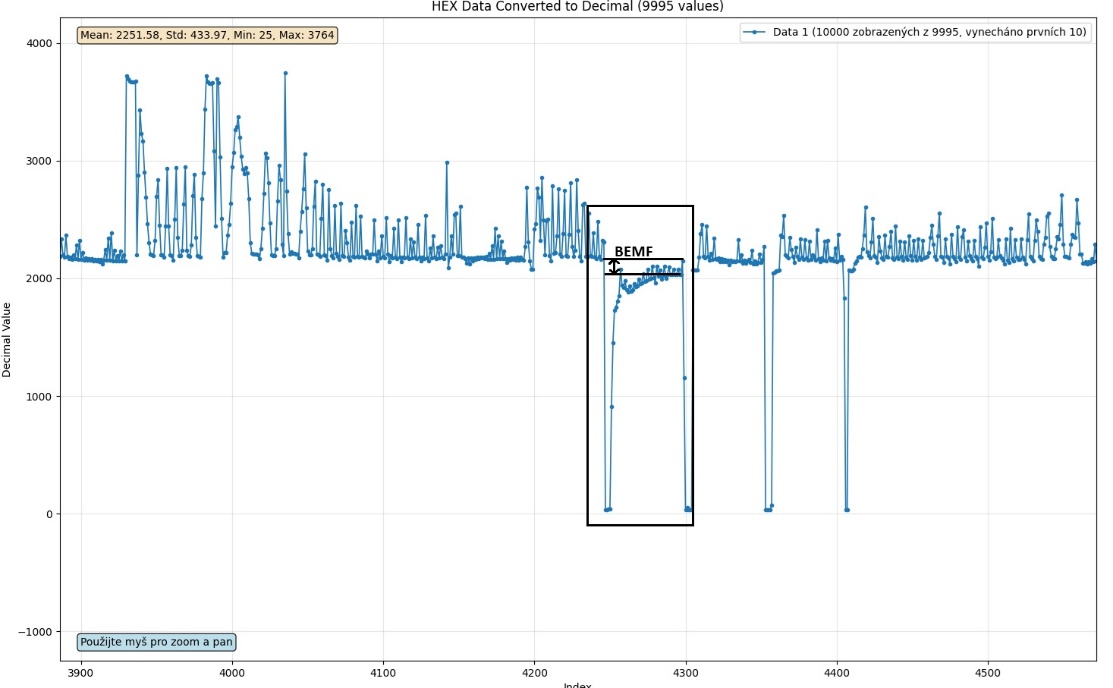
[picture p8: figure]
Obsah obrázku text, diagram, snímek obrazovky, řada/pruh Obsah generovaný pomocí AI může být nesprávný.

Na následujícím měření je vidět chování motoru při mechanickém dorazu. V tomto stavu se výrazně mění průběh napětí na vinutí a hodnota zpětné elektromotorické síly (BEMF) je oproti normálnímu chodu motoru znatelně menší. Tento jev lze využít k detekci dorazu a tím i k rozpoznání omezení pohybu motoru.

Obrázek 6: detekce BEMF při dorazu

# 5. Plánované úpravy a optimalizace

V rámci dalších kroků vývoje je plánováno provést úpravy hardwaru, zejména odstranit dočasná řešení realizovaná pomocí drátování a navrhnout kompletní desku, na které bude měřicí modul integrován přímo s řídicí částí. Na úrovni firmwaru bude potřeba doladit algoritmus detekce dorazů a správné zapisování hodnot do registrů pro čtení pomocí modbus,

# 6. Závěr

V aktuálním stavu, již zařízení spolehlivě zajišťuje detekci kroků i směru otáčení motoru a je také možnost rozpoznávání mikrokoků. Funkce detekce dorazů je v tuto chvíli rozpracovaná a postupně se dolaďuje, aby byla použitelná i v praktických aplikacích. Co se týče komunikace přes Modbus, ta je již funkční, je však potřeba ještě upravit strukturu registrů a případně doplnit možnost přenosu celého bufferu naměřených hodnot. Díky tomu by bylo možné snadno vykreslit kompletní průběhy signálů a dále tak analyzovat chování motoru.

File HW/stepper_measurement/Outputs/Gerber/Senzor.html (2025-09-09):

Altium

# Design Rule Verification Report

Date: | | 28.03.2025
Time: | | 9:23:24
Elapsed Time: | | 00:00:03
Filename: | | C:\Users\rousa\Documents\jablotron\stepper_measurement\HW\stepper_measurement\stepper_measuremnt_senzor\Senzor.PcbDoc

Warnings: | | 0
Rule Violations: | | 0

## Summary

Warnings | Count
Total | 0

Rule Violations | Count
Clearance Constraint (Gap=5.906mil) (All),(All) | 0
Short-Circuit Constraint (Allowed=No) (All),(All) | 0
Un-Routed Net Constraint ( (All) ) | 0
Modified Polygon (Allow modified: No), (Allow shelved: No) | 0
Width Constraint (Min=5.906mil) (Max=196.85mil) (Preferred=5.906mil) (All) | 0
Power Plane Connect Rule(Direct Connect )(Expansion=19.685mil) (Conductor Width=9.842mil) (Air Gap=9.842mil) (Entries=4) (IsVia) | 0
Power Plane Connect Rule(Relief Connect )(Expansion=5.906mil) (Conductor Width=5.906mil) (Air Gap=5.906mil) (Entries=4) (All) | 0
Minimum Annular Ring (Minimum=5.906mil) (All) | 0
Hole Size Constraint (Min=11.811mil) (Max=3937.008mil) (All) | 0
Hole To Hole Clearance (Gap=11.811mil) (All),(All) | 0
Minimum Solder Mask Sliver (Gap=10mil) (Disabled)(All),(All) | 0
Silk To Solder Mask (Clearance=10mil) (Disabled)(IsPad),(All) | 0
Silk to Silk (Clearance=10mil) (Disabled)(All),(All) | 0
Net Antennae (Tolerance=0mil) (All) | 0
Height Constraint (Min=0mil) (Max=1000mil) (Prefered=500mil) (All) | 0
Total | 0

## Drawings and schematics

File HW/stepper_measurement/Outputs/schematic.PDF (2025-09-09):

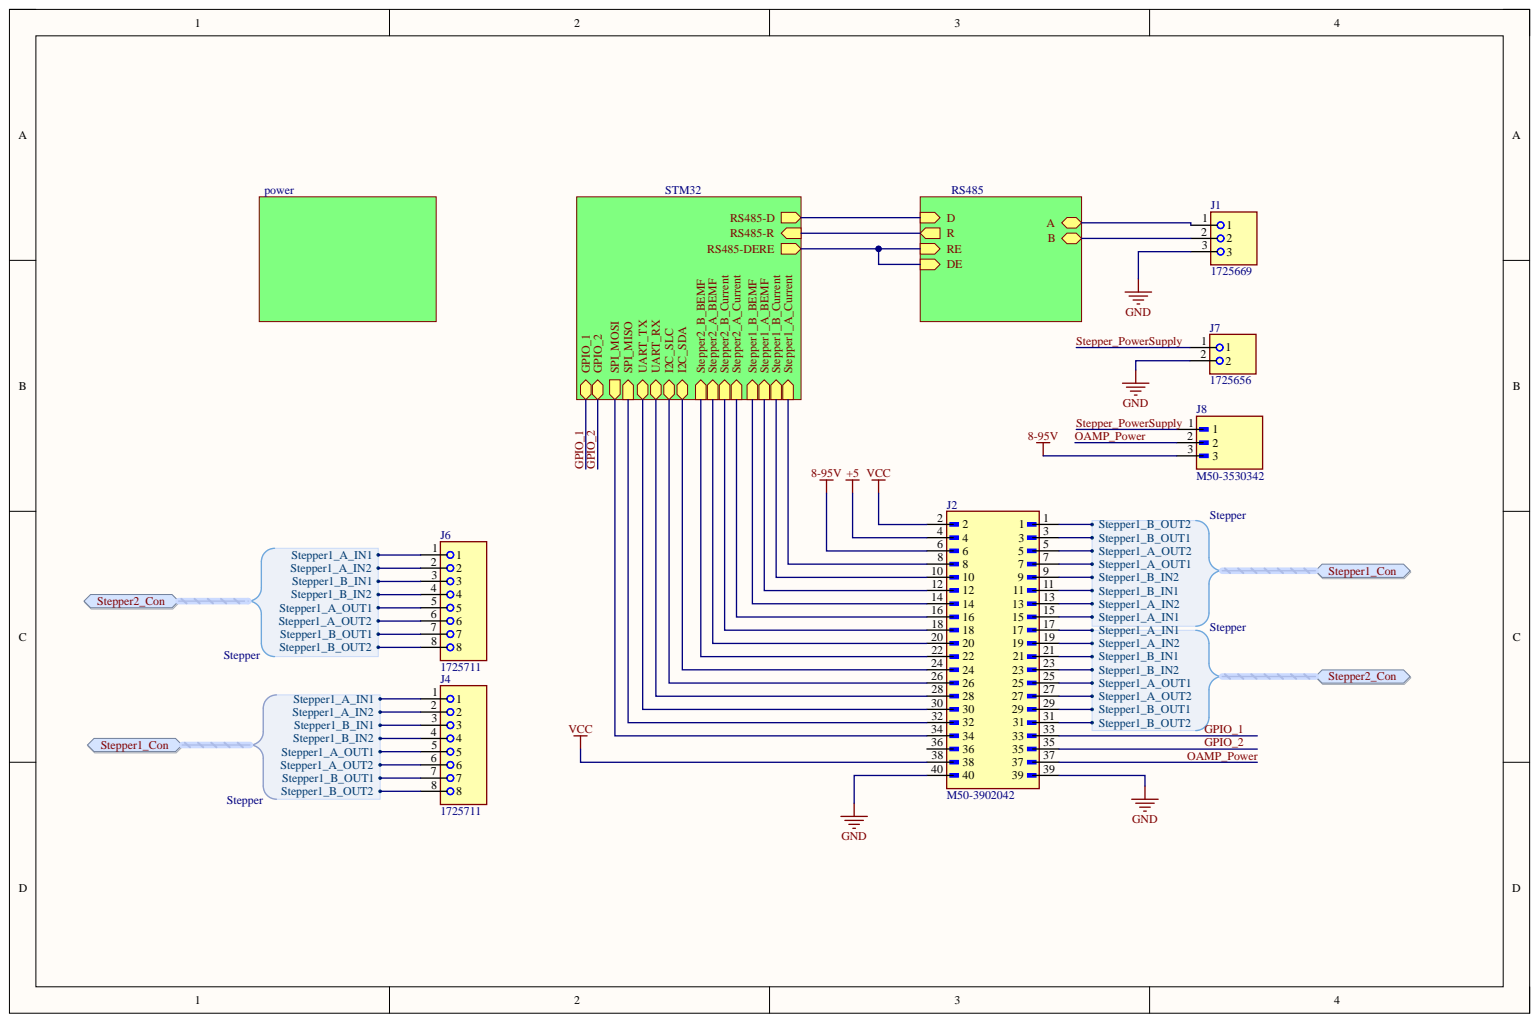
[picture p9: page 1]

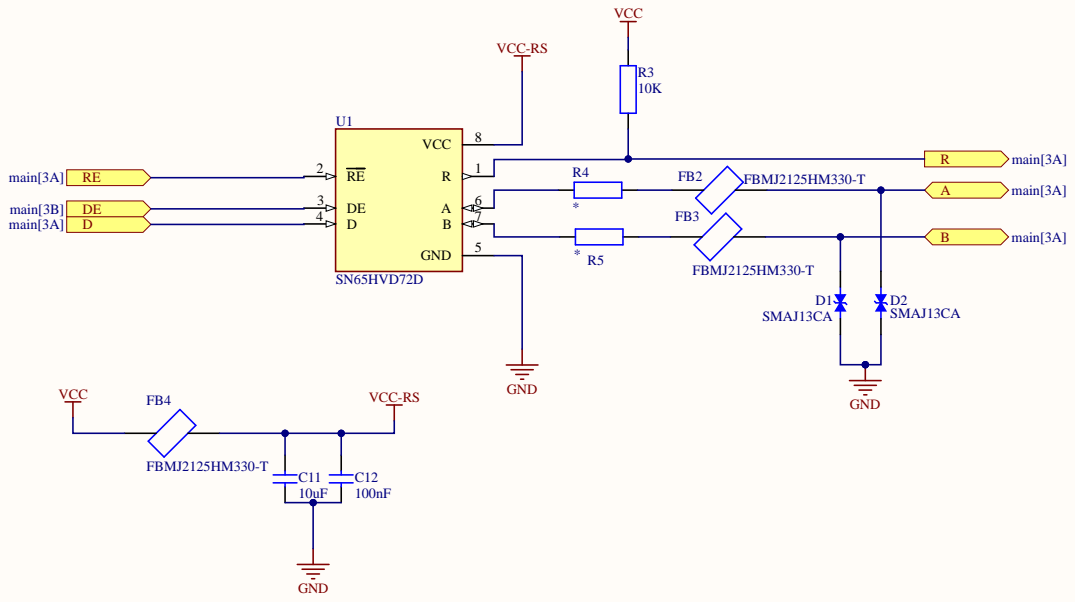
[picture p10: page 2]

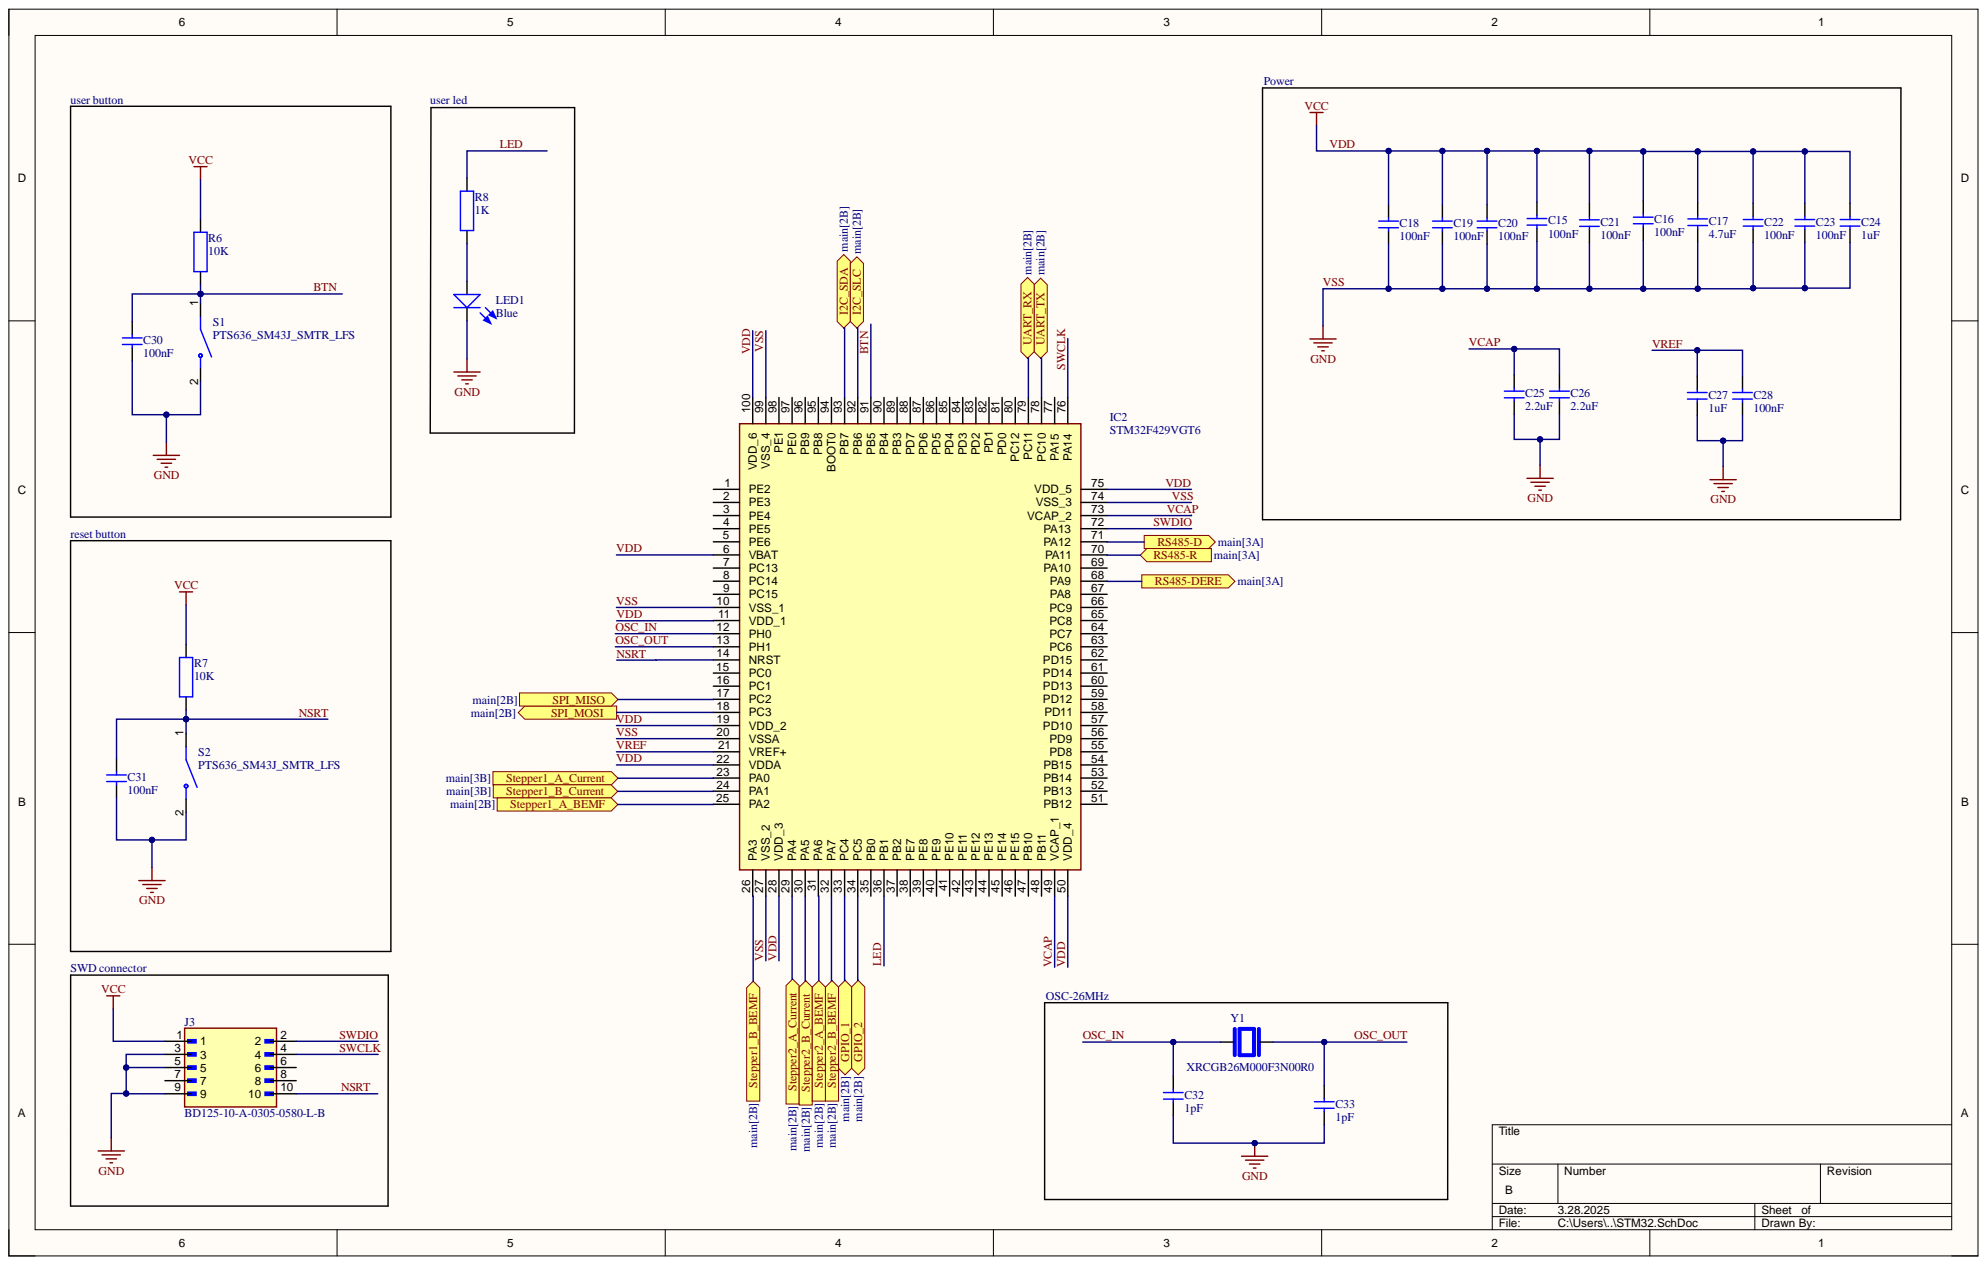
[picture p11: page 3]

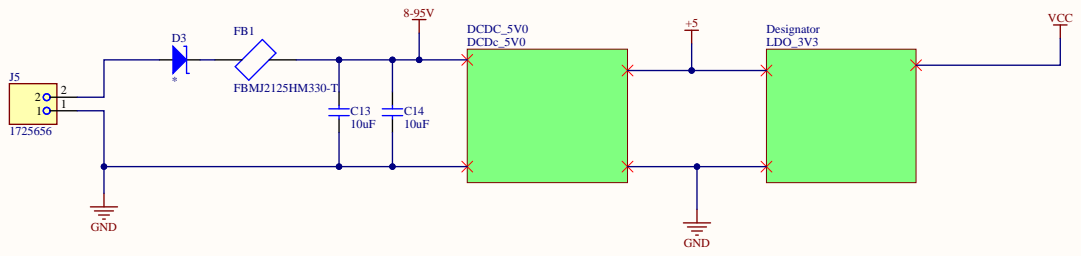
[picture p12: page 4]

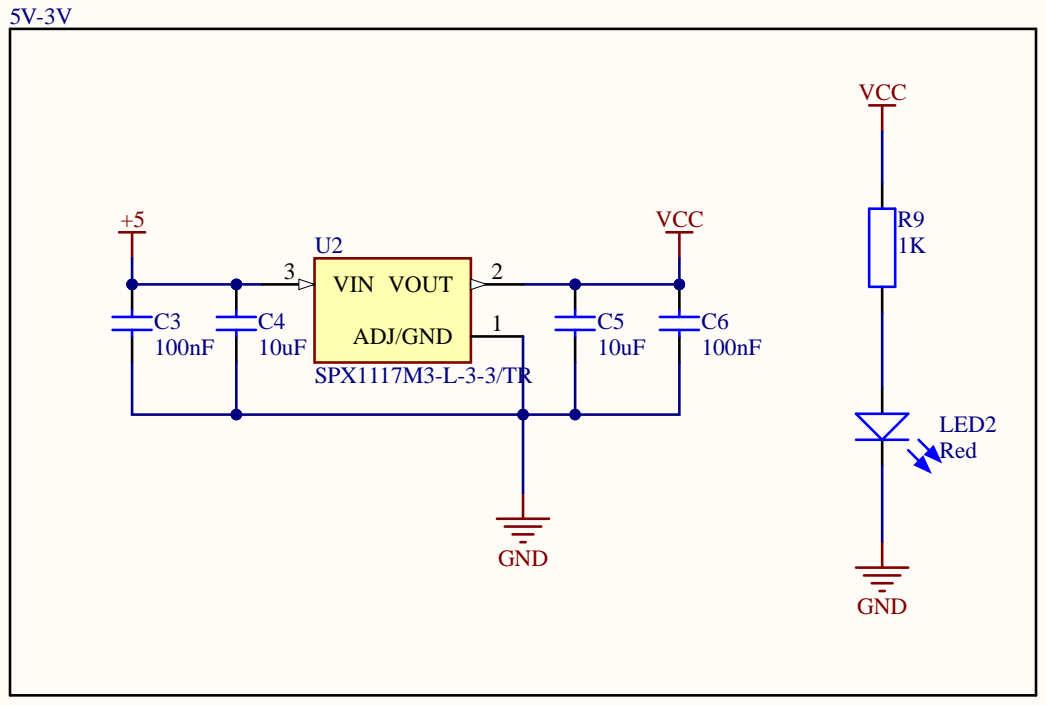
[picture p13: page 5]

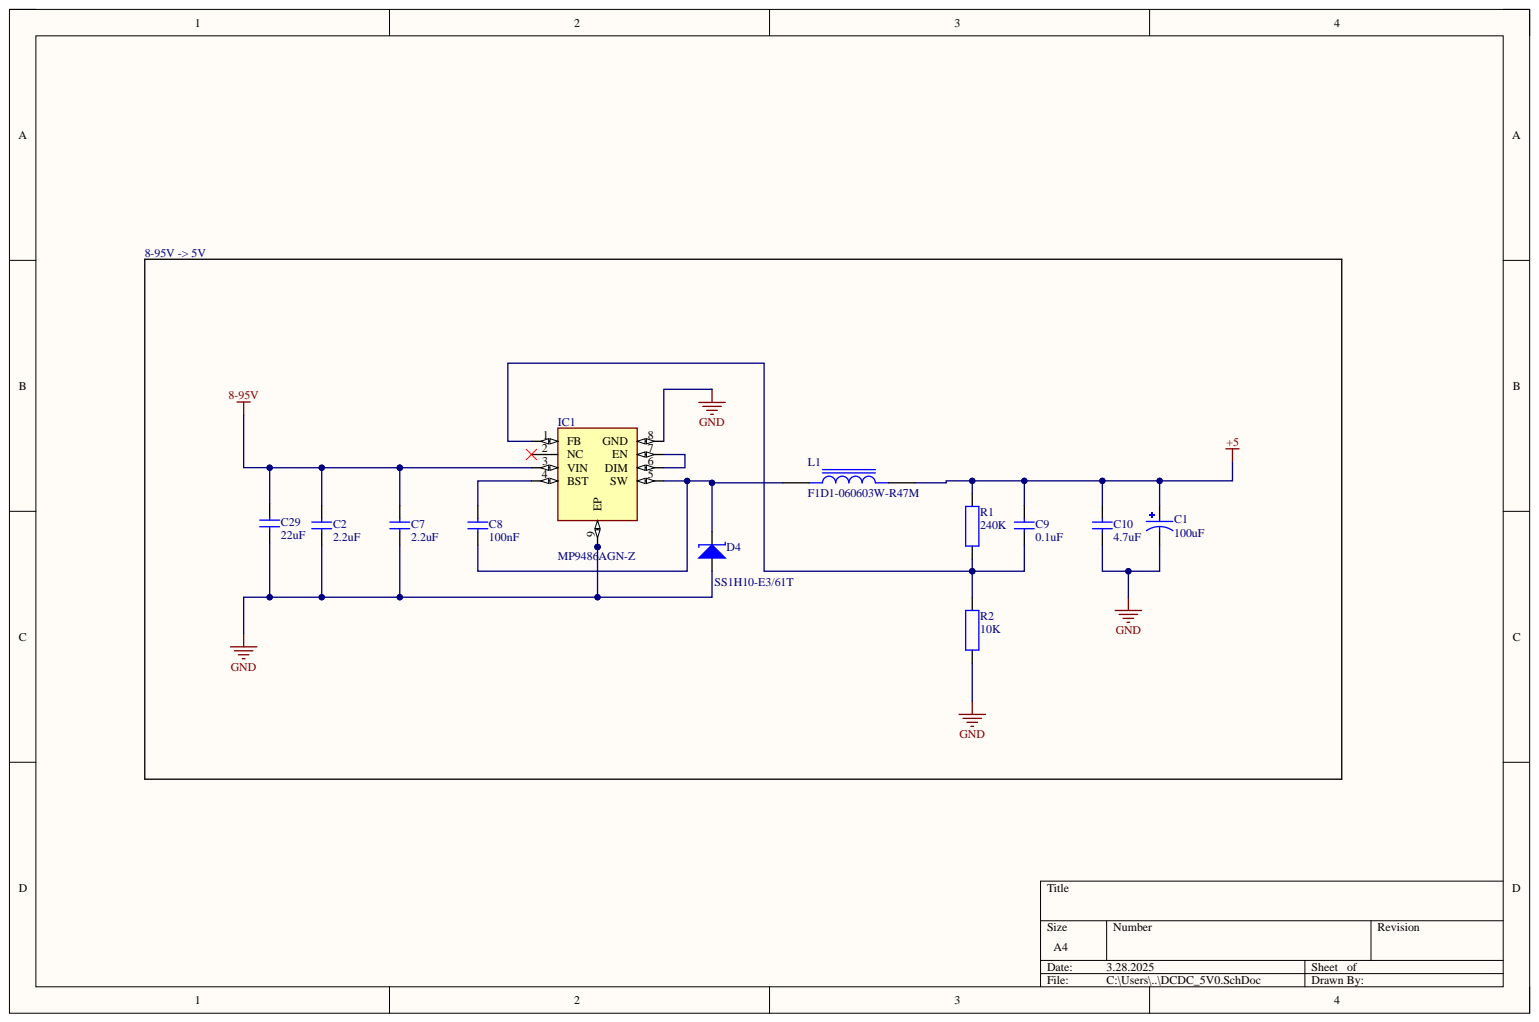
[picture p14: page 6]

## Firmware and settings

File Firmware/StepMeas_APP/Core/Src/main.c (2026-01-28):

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
/* Includes ------------------------------------------------------------------*/
#include "main.h"

/* USER CODE BEGIN Includes */
#include "common.h"
#include "modbus_slave.h"
#include "configuration.h"
#include "mb_upgrade.h"
#include "system_msp.h"
#include "control.h"
#include "flash_app.h"
#include "voltage_current_probe.h"
#include "switch.h"

/* USER CODE END Includes */

/* USER CODE BEGIN PD */
#define PERIOD_HANDLE_MED_PRIO      5
#define PERIOD_HANDLE_LOW_PRIO      50

/* USER CODE END PD */

ADC_HandleTypeDef hadc1;
DMA_HandleTypeDef hdma_adc1;

CRC_HandleTypeDef hcrc;

I2C_HandleTypeDef hi2c1;

IWDG_HandleTypeDef hiwdg;

SPI_HandleTypeDef hspi2;

TIM_HandleTypeDef htim2;

UART_HandleTypeDef huart5;

/* USER CODE BEGIN PV */
uint32_t max_low = 0;
uint32_t max_med = 0;

/* USER CODE END PV */

void SystemClock_Config(void);
static void MX_GPIO_Init(void);
static void MX_DMA_Init(void);
static void MX_I2C1_Init(void);
static void MX_SPI2_Init(void);
static void MX_UART5_Init(void);
static void MX_CRC_Init(void);
static void MX_TIM2_Init(void);
static void MX_IWDG_Init(void);
static void MX_ADC1_Init(void);
/* USER CODE BEGIN 0 */
char uart_buf[50];
uint32_t adc_valuess;

/* USER CODE END 0 */

/**
 * @brief  The application entry point.
 * @retval int
 */
int main(void)
{

    /* USER CODE BEGIN 1 */
    Status_t ret = STATUS_OK;
    uint32_t tick_med = 0;
    uint32_t tick_slow = 0;
    uint32_t start = 0;

    /* Remap reset vector and enable interrupts */
    System_RemapApplicationVector();
    __enable_irq();

    /* USER CODE END 1 */

    /* MCU Configuration--------------------------------------------------------*/

    /* Reset of all peripherals, Initializes the Flash interface and the Systick. */
    HAL_Init();

    /* USER CODE BEGIN Init */
    HAL_RCC_DeInit();
    /* USER CODE END Init */

    /* Configure the system clock */
    SystemClock_Config();

    /* USER CODE BEGIN SysInit */
    //MX_USART1_UART_Init();
    /* USER CODE END SysInit */

    /* Initialize all configured peripherals */
    MX_GPIO_Init();
    MX_DMA_Init();
    MX_I2C1_Init();
    MX_SPI2_Init();
    MX_UART5_Init();
    MX_CRC_Init();
    MX_TIM2_Init();
    MX_IWDG_Init();
    MX_ADC1_Init();
    /* USER CODE BEGIN 2 */
    Switch_Init();
    /* Initialize system modules */
    ret |= System_InitWdg();
    ret |= System_ReloadWdg();
    System_CrcInit();
    ret |= Config_Init();
    ret |= Control_Init();

    /* Initialize flash memory module */
    ret |= FlashApp_Init();

    /* Initialize communication modules */
    ret |= MbSlave_Init();

    /* Initialize test modules */
    /* TODO */
    Probe_Init();
    Probe_InitOffset();
    /* Reload watchdog and check for errors in the initialization process */
    ret |= System_ReloadWdg();

    // CHECK_ERROR(ret, ERROR_CODE_init);
    tick_med = HAL_GetTick();
    tick_slow = HAL_GetTick();

    /* Initialize Modbus upgrade module */
    /* USER CODE END 2 */

    /* Infinite loop */
    /* USER CODE BEGIN WHILE */
    while (1)
    {
        /* High priority - real-time handles */
        MbSlave_Handle();

        /* Medium priority - fast handles */
        if (TICK_EXPIRED(tick_med))
        {
            tick_med += PERIOD_HANDLE_MED_PRIO;
            start = HAL_GetTick();

            /* Test modules handles */
            /* TODO */

            /* Medium priority time measurement */
            max_med = MAX(max_med, HAL_GetTick() - start);
        }

        /* Low priority - slow handles */
        if (TICK_EXPIRED(tick_slow))
        {

            tick_slow = HAL_GetTick() + PERIOD_HANDLE_LOW_PRIO;
            start = HAL_GetTick();

            /* Communication handles */
            ret |= Control_Handle();
            ret |= MbSlave_UpdateSlaveAddress();

            /* Flash memory handle */
            ret |= FlashApp_Handle();

            /* Test modules handles */
            /* TODO */

            /* Low-priority time measurement */
            max_low = MAX(max_low, HAL_GetTick() - start);

            /* Watchdog reload */
            ret |= System_ReloadWdg();
            HAL_GPIO_TogglePin(led_GPIO_Port, led_Pin);
            conf.sys.io_input = Switch_GetAll();
            MbSlave_UpdateSlaveAddress();

        }

        /* Check for general error in while loop */
//    CHECK_ERROR(ret, ERROR_CODE_while);
        /* USER CODE END WHILE */

        /* USER CODE BEGIN 3 */
    }
    /* USER CODE END 3 */
}

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
/* USER CODE BEGIN 4 */
/**
 * @brief  Callback funkce po dokončení ADC konverze (DMA).
 */
void HAL_TIM_PeriodElapsedCallback(TIM_HandleTypeDef *htim)
{
    if (htim->Instance == TIM2)
    {

        StartAdcMeasurement();

    }
}
void HAL_UART_TxCpltCallback(UART_HandleTypeDef *huart)
{
    MbSlave_TxCpltCallback(huart);
}
void HAL_UART_RxCpltCallback(UART_HandleTypeDef *huart)
{
    MbSlave_RxCpltCallback(huart);
}

void HAL_UART_ErrorCallback(UART_HandleTypeDef *huart)
{
    MbSlave_ErrorCallback(huart);
}

/* USER CODE END 4 */
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


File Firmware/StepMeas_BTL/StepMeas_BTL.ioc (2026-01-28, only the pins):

Mcu.UserName=STM32F446RETx
PA1.Signal=ADCx_IN1
PA12.Signal=GPIO_Output
PA13.Signal=SYS_JTMS-SWDIO
PA14.Signal=SYS_JTCK-SWCLK
PA2.Signal=ADCx_IN2
PA3.Signal=ADCx_IN3
PA4.Signal=ADCx_IN4
PA5.Signal=ADCx_IN5
PA6.Signal=ADCx_IN6
PA7.Signal=ADCx_IN7
PB0.Signal=ADCx_IN8
PB10.Signal=SPI2_SCK
PB12.Signal=GPIO_Output
PB13.Signal=GPXTI13
PB6.Signal=I2C1_SCL
PB7.Signal=I2C1_SDA
PC1.Signal=SPI2_MOSI
PC12.Signal=UART5_TX
PC13.Signal=GPIO_Output
PC14-OSC32_IN.Signal=GPIO_Output
PC15-OSC32_OUT.Signal=GPIO_Output
PC2.Signal=SPI2_MISO
PD2.Signal=UART5_RX
PH0-OSC_IN.Signal=RCC_OSC_IN
PH1-OSC_OUT.Signal=RCC_OSC_OUT

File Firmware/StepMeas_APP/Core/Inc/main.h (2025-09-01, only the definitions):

#define led_Pin GPIO_PIN_12
#define led_GPIO_Port GPIOB
#define button_Pin GPIO_PIN_13
#define button_GPIO_Port GPIOB
#define button_EXTI_IRQn EXTI15_10_IRQn

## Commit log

2025-05-13 ADD: Copy of project from RTD emulator.
    [StepperMeas.xlsm, configuration.h]
2025-05-27 MOD: removing redundant files
    [configuration.h]
2025-05-27 MOD: REM: reg_map
    [StepperMeas.xlsm]
2025-05-27 MOD: main, UART RX capture
    [StepperMeas.xlsm]
2025-09-01 MOD: cleanup
    [configuration.h]
2025-09-01 MOD: ADC 8ch measuring
2025-09-08 ADD: switch.c , swtich.h
2025-09-09 MOD: working address switch,Enable final ADC channel
2025-09-09 ADD: HW mainBoard
    [DCDC_5V0.SchDoc, LDO_3V3.SchDoc, RS485.SchDoc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]
2025-09-09 ADD: HW senzor
    [CurrentSensor.SchDoc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]
2025-09-09 MOD: Fix ADC routing to correct pin
    [STM32.SchDoc]
2025-09-15 MOD: Refined filtering
2025-09-15 MOD: dual motor reading
2025-09-25 MOD: Fix voltage detection
    [voltage_current_probe.c]
2025-09-25 MOD: Improve voltage detection
2025-09-25 MOD: fix voltage sinus2
    [voltage_current_probe.c]
2025-09-30 MOD: odstraněnní buggu (zpožděné načítání hodnot, + posun logování)
    [voltage_current_probe.c]
2025-10-02 MOD: plně fukční detekce dorazu motoru, krokování pro jden motor
2025-10-13 MOD: detekce kroků i na novém motoru
2025-10-13 MOD: částečná detekce dorazu na novým motoru
2025-10-14 MOD: lepší buffrování a vyhodnocování dorazu na novém motoru
2025-10-16 MOD: zapis na adresy pro čtení z modbus
    [StepperMeas.xlsm]
2025-11-03 ADD: HW desky verze 2
    [CurrentSenzor.SchDoc, DCDC_5V0.SchDoc, LDO_3V3.SchDoc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]
2025-12-08 uprava ADC pro novou verzi PCB
2026-01-20 odebrání test složky , přidání start inicializace( nastavení hladin ADC podle napájecího napětí )
    [AFL2018 (sorted alpha teams).csv, AFL2018 (sorted pts and %).csv, params.txt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]
2026-01-28 MOD: odstranění bugu (start APP po bootu)
    [main.c]
2026-01-29 MOD: úprava parametrů pro starší motor na detekci dorazu

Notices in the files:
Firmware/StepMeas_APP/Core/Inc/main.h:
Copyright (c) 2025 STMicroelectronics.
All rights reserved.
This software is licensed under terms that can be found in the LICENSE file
